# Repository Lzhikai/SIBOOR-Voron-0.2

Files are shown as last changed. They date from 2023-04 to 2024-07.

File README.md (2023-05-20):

# SIBOOR-V0.2

### 0.2-LED-Wiring ：About the wiring of the sibor kit to the hot-side LED.
### Metalsupplements ： Print files not included in the CNC version.
### supplementary ： Unlike the official installation documentation, the installation needs to be done in conjunction with the official documentation and our documentation.

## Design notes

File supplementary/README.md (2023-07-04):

# This guide covers the differences between the SIBOOR 0.2kit and the original VORON0.2 tutorial, and includes instructions on wiring and debugging.
# The supplement also contains the differences section of Siboor V0.2. updated 2023/7/4
# You can download and view the official PDF assembly tutorial of VORON here：[Voron-0.2/Manuals](https://github.com/VoronDesign/Voron-0/tree/Voron0.2/Manuals)  · GitHub
***Github SIBOOR V0.1 kit assembly manual instruction.***

* Page 13-15  ：In SIBOOR V0.2 kit, EXTRUSION A and EXTRUSION B are combined into one EXTRUSION, both of which have been tapped and are common to each other. C EXTRUSION and H EXTRUSION are combined into one EXTRUSION, both of which are drilled and tapped, which are common to each other.

* Page18 ：The SIBOOR V0.2 kit uses the guide strip of purple PCB, so it does not need to use the printed parts and embedded M2 nut.

* Page23 ：SIBOOR V0.2 kit is not equipped with NO DROP NUTS

* Page 20、24 和 113  ：As described above, two purple PCBs are used as guide rail fixing strips to fix the MGN7 guide rail.

* Page 48  ： The SIBOOR V0.2 kit is already equipped with a soldered Endstop, plug and play.

* Page154 ：Make sure that the bearing is flush with the shaft, otherwise it will cause friction between the metal shaft and the motor. Place the side of the bearing flat on the table and press the white gear with both thumbs to make the bearing flush with the shaft.

* Page126 ：In addition to using double-sided adhesive tape to fix the power supply, you can also choose to install two M3 × 6 screws on the reverse side to fix the power supply.

* Page142 ：For SIBOOR V0.2 kit, the heating bed has already lifted the prefabricated fuse. please skip this step

* Page173 ：Use 4 pieces of M2.5×8 screws to fix the CHC V6 hot end

* Page 184  ：SIBOOR V0.2 kit, using a two in one Gemini motherboard, using four nylon posts and M3 × 8 Screws are fixed on the acrylic panel.

* Page 199- 205 ：See the SIBOOR V0.2 kit supplementary instructions separatel

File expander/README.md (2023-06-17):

[Voron-Hardware_STM32_Mini12864](https://github.com/VoronDesign/Voron-Hardware/tree/master/STM32_Mini12864)
# Modified by Wind zhu  , expander.stl
### 3(1mm).stl and 3(2mm).stl are optional.
### just choose one of them to print as 1mm may be too thin and bend easily, the choice is yours

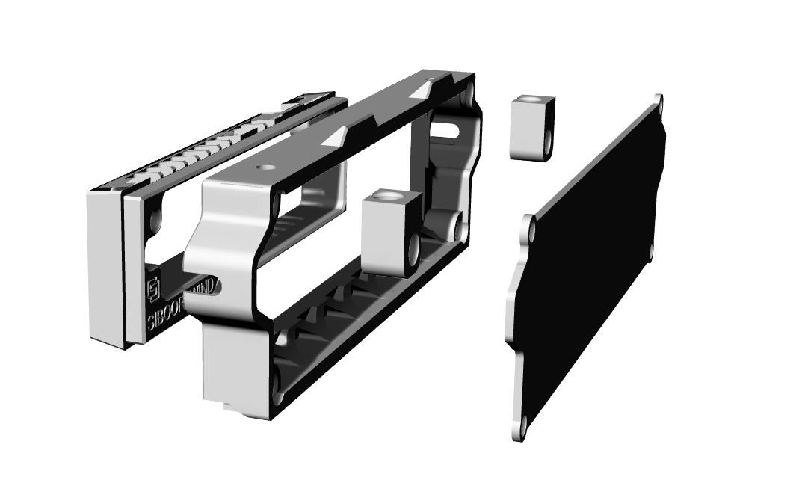
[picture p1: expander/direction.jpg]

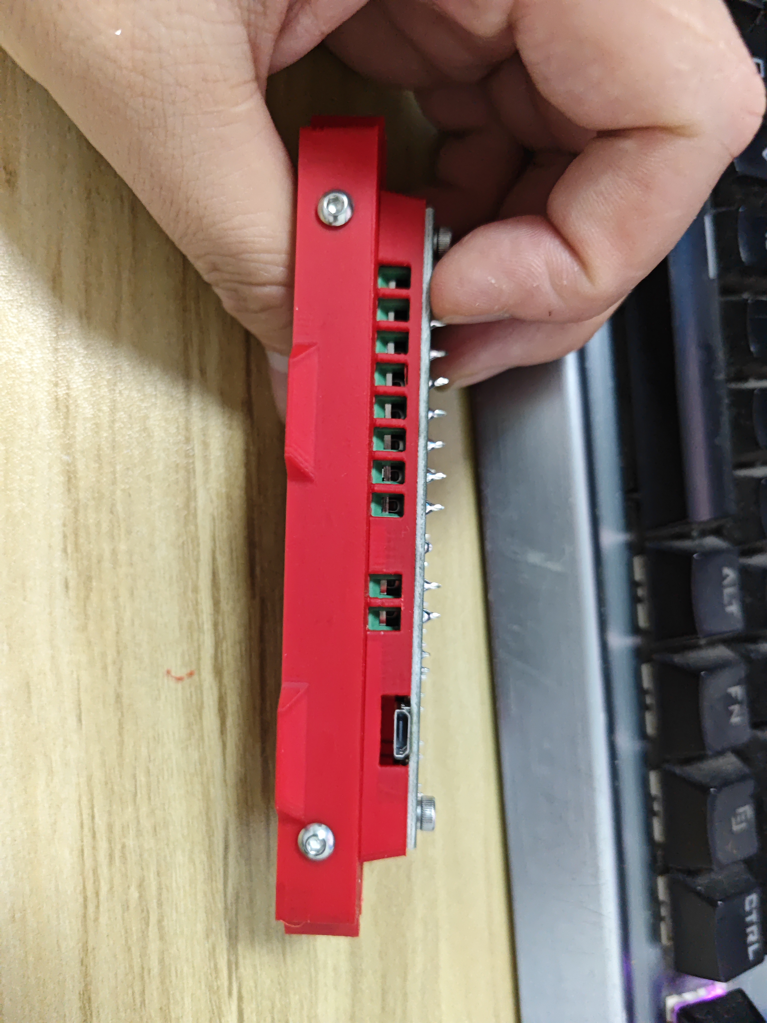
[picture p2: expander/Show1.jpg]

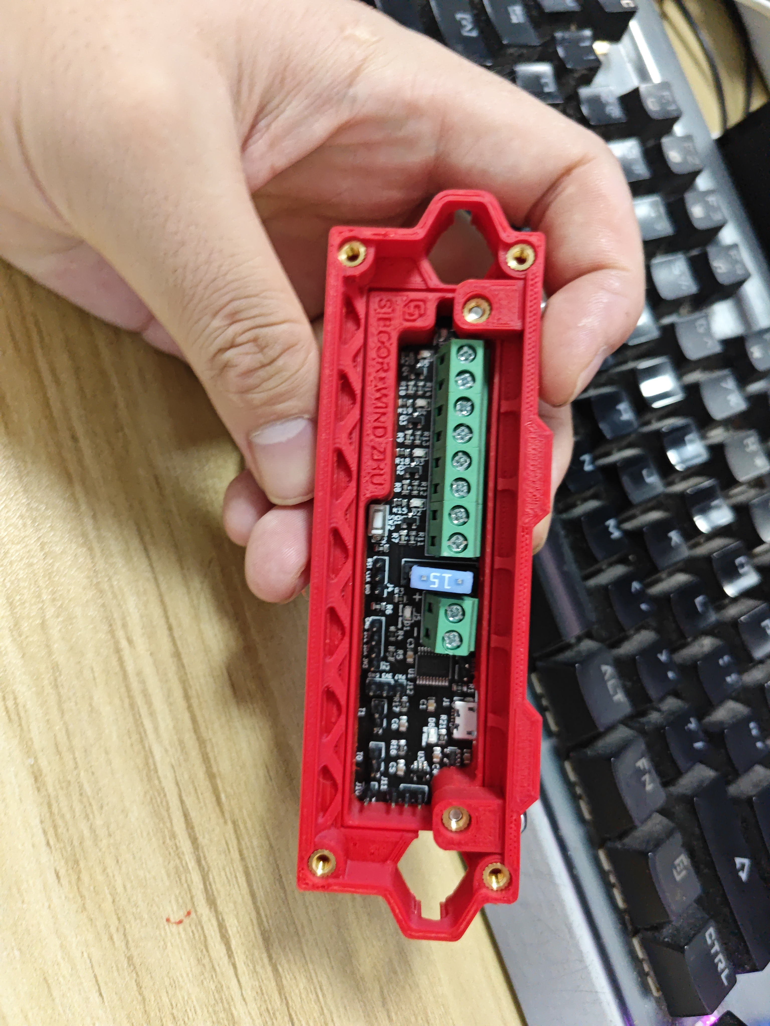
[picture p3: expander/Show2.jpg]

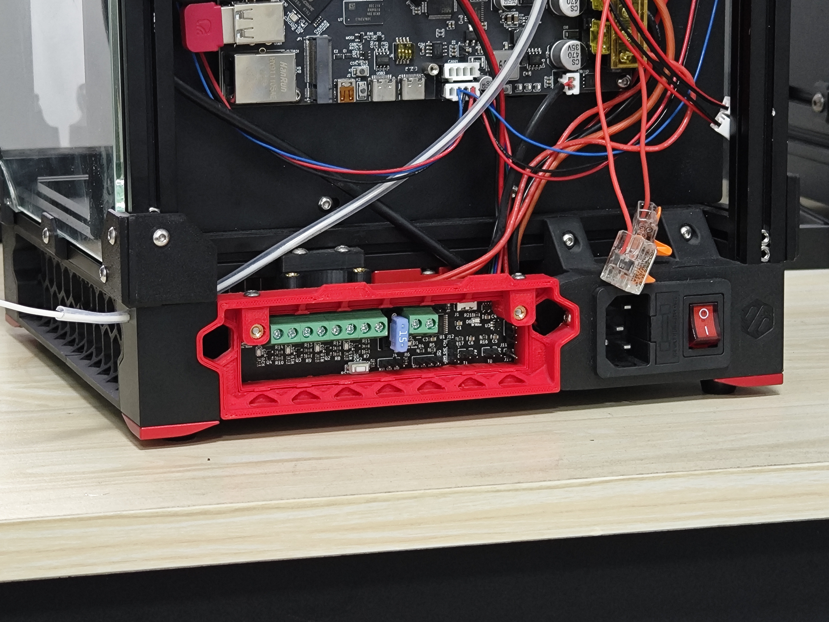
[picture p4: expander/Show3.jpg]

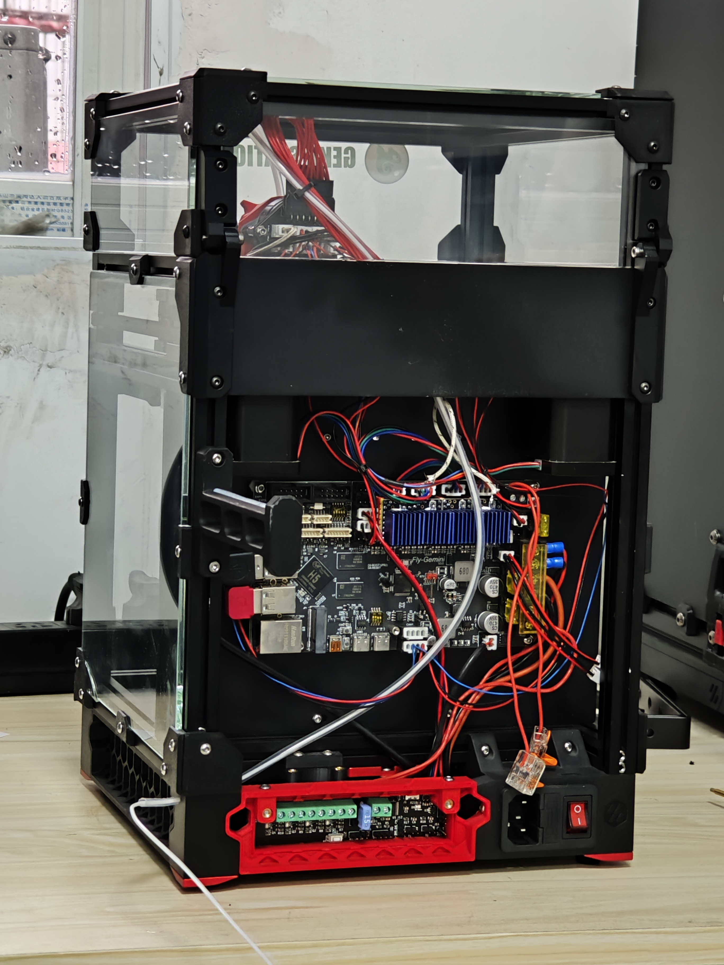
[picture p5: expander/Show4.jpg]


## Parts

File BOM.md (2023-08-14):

# SIBOOR-Voron 0.2 R1 Bom list 
### This list only for reference.  
### Under special situations, parts will updated to same level and quality products.  
### If there has any changes, will update immediately here.
## VORON 0.2 R1 Revision 1.2

| Category | Description | brand | Qty | update time |
|---|---|---|-----|---|
| R1 version | Micro Switch with cable | SIBOOR | 1 | 7/3/23 |
| R1 version | MR85 Bearing | SIBOOR | 1 | 7/3/23 |
| other | Metal rail fixing strip | SIBOOR | 5 | 5/10/23 |
| other | Custom High Speed Steel M1.5/M2.0/ Cross Screwdriver | SIBOOR | 1 | 5/10/23 |
| other | Mini Stealthburner LED light（2 meters with PTFE leads） | SIBOOR | 1 | 4/19/23 |
| other | One out two fan extension cable（PTFE） | / | 1 | 4/21/23 |
| other | Black M3 Metal Internal Thread Stud | / | 2 | 4/1/23 |
| other | Allen wrench (one M2/M3 each) | / | 1 | 3/1/23 |
| Fasteners | 3x6x0.5 Shim Washer | Nickel plating 10.9 | 55  | 4/17/23 |
| Fasteners | M2 Nut | Nickel plating 10.9 | 64  | 3/1/23 |
| Fasteners | M3 Nut | Nickel plating 10.9 | 161 | 3/1/23 |
| Fasteners | M2x6 SHCS | Nickel plating 10.9 | 81  | 3/1/23 |
| Fasteners | M2x6 FHCS | Nickel plating 10.9 | 12  | 3/1/23 |
| Fasteners | M2x8 SHCS | Nickel plating 10.9 | 12  | 3/1/23 |
| Fasteners | M3x6 BHCS | Nickel plating 10.9 | 54  | 3/1/23 |
| Fasteners | M3x8 BHCS | Nickel plating 10.9 | 133 | 3/1/23 |
| Fasteners | M3x8 FHCS | Nickel plating 10.9 | 6 | 3/1/23 |
| Fasteners | M3x10 BHCS | Nickel plating 10.9 | 50  | 4/17/23 |
| Fasteners | M3x12 BHCS | Nickel plating 10.9 | 29  | 3/1/23 |
| Fasteners | M3x16 BHCS | Nickel plating 10.9 | 12  | 3/1/23 |
| Fasteners | M3x25 BHCS | Nickel plating 10.9 | 12  | 3/1/23 |
| Fasteners | M3x30 BHCS | Nickel plating 10.9 | 12  | 3/1/23 |
| Fasteners | M3x35 BHCS | Nickel plating 10.9 | 35  | 3/1/23 |
| Fasteners | M3x40 BHCS | Nickel plating 10.9 | 12  | 3/1/23 |
| Fasteners | M2x10 Self Tapping Screws for Plastic | Nickel plating 10.9 | 35  | 3/1/23 |
| Fasteners | M3 Brass heatstake inserts - short M3x5x4 | / | 58  | 3/1/23 |
| Fasteners | M3 t-nut | / | 2 | 3/1/23 |
| Fasteners | F623-RS Bearing | / | 24  | 3/1/23 |
| Fasteners | yellow die springs 8x4x20mm | / | 3 | 3/1/23 |
| Fasteners | Little Rubber Feet | / | 4 | 3/1/23 |
| Fasteners | 6mm x 3mm Round Neodymium Magnets | / | 8 | 3/1/23 |
| Fasteners | Hexagonal nylon screw post | / | 4 | 3/1/23 |
| Fasteners | BMG Extruder Kit（30 teeth reduction gear is SIboor CNC version） | / | 1 | 8/1/23 |
| Frame | EXTRUSION 15x15 200mm | SIBOOR | 16  | 3/1/23 |
| Frame | EXTRUSION 15x15 100mm | SIBOOR | 3 | 3/1/23 |
| Electronics | LM200-20B24R2 200W Power |  Mornsun | 1 | 3/1/23 |
| Electronics | Gemini V3 board | Mellow | 1 | 3/1/23 |
| Electronics | TMC2209 drivers | / | 4 | 3/1/23 |
| Electronics | SanDisk MicroSD Card 32GB | Sandisk | 1 | 3/1/23 |
| Electronics | USB WIFI module | Tencent | 1 | 3/1/23 |
| Electronics | NEMA14 Stepper Motor 40Ncm | SIBOOR | 2 | 3/1/23 |
| Electronics | NEMA17 Stepper Motor w/ integrated lead screw 200mm T8x8 | SIBOOR | 1 | 3/1/23 |
| Electronics | NEMA14 36mm pancake Motor with 10 tooth gear | MOON‘S | 1 | 3/1/23 |
| Electronics | 3010 blower fans 24V | GEEK | 2 | 3/1/23 |
| Electronics | 3010 axial fan 24V | GEEK | 2 | 3/1/23 |
| Electronics | Micro Switch with cable | / | 1 | 3/1/23 |
| Electronics | C13 Power Cord | / | 1 | 3/1/23 |
| Electronics | IEC320 C14 inlet | / | 1 | 3/1/23 |
| Electronics | CHC V6 Hotend | SIBOOR | 1 | 3/1/23 |
| Electronics | V0-Display | SIBOOR | 1 | 3/1/23 |
| Electronics | 3M 5952 VHB tape | / | 1 | 3/1/23 |
| Electronics | High Flex Wire 20gauge | / | 2 | 3/1/23 |
| Electronics | 7mm x 7mm cable chain (less than 1/2 meter needed) | / | 1 | 3/1/23 |
| Electronics | ADXL345 | SIBOOR | 1 | 3/1/23 |
| Electronics | PTFE cable 0.5M | SIBOOR | 1 | 7/3/23 |
| Electronics | Nylon Cable Ties (1.8mm wide or smaller) | / | 50  | 3/1/23 |
| Motion | MGN7H Linear Rail with Carriage - 150mm(nickel plated) | SIBOOR | 5 | 4/1/23 |
| Motion | GT2 20T (5mm ID 6mm W) | SIBOOR | 2 | 3/1/23 |
| Motion | GT2 Open Belt (6mm W) - 3000mm | GATES | 3 | 3/1/23 |
| Motion | Silicone DC 24V Heater 100x100mm 60W | SIBOOR | 1 | 3/1/23 |
| Buildplate | PEI + 3M 468MP (200MP) | SIBOOR | 1 | 3/1/23 |
| Panels | Acrylic Sheet Clear - 212x230x3mm | / | 2 | 3/1/23 |
| Panels | Acrylic Sheet Clear - 212x239x3mm | / | 1 | 3/1/23 |
| Panels | Upper Rear Panel 212x63x3mm | / | 1 | 3/1/23 |
| Panels | Lower Rear Panel 212x185x3mm | / | 1 | 3/1/23 |
| Panels | Deck Panel 3mm thick (See DXF) | / | 1 | 3/1/23 |
| Panels | Motor Panel 3mm thick (See DXF) | / | 1 | 3/1/23 |
| Panels | Bottom Panel 3mm thick (See DXF) | / | 1 | 3/1/23 |
| Panels | Mid Panel 3mm thick (See DXF) | / | 1 | 3/1/23 |
| Misc. | Bowden Tube 4x2mm - 1m | / | 1 | 3/1/23 |
| Misc. | Bowden Tube 4x3mm - 1m | / | 1 | 3/1/23 |
| Extrusion Tophat | Top Panel 212x212mm | / | 1 | 3/1/23 |
| Extrusion Tophat | Side Panels 212x71mm | / | 4 | 3/1/23 |
| Extrusion Tophat |  EXTRUSION 15x15 200mm | SIBOOR | 4 | 3/1/23 |
| Extrusion Tophat | EXTRUSION15x15×80mm | SIBOOR | 4 | 3/1/23 |
| prints | Full set of prints（ABS） | R1 version | 1 | 4/20/23 |

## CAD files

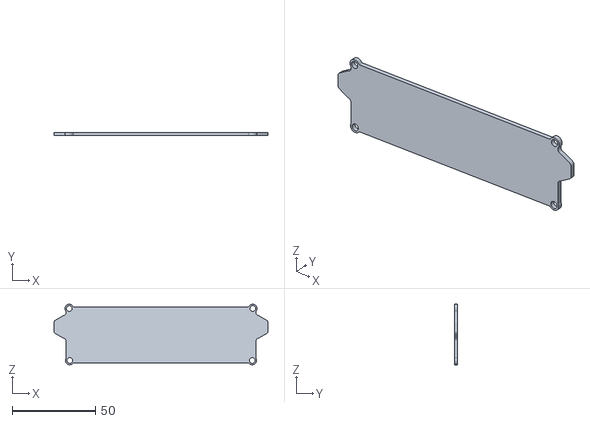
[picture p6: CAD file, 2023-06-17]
expander/3(2mm).stl
128.5 x 2.08 x 36.4

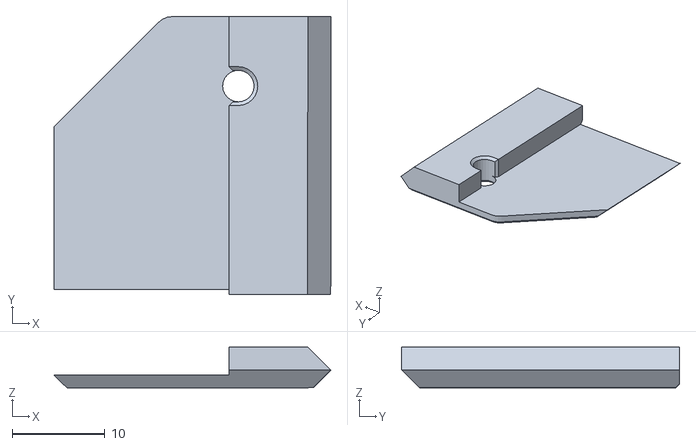
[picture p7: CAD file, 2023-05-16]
Metalsupplements/Panel_Mounting/Rear_Bottom_Right_Clip_x1.stl
29.9 x 30.0 x 4.42

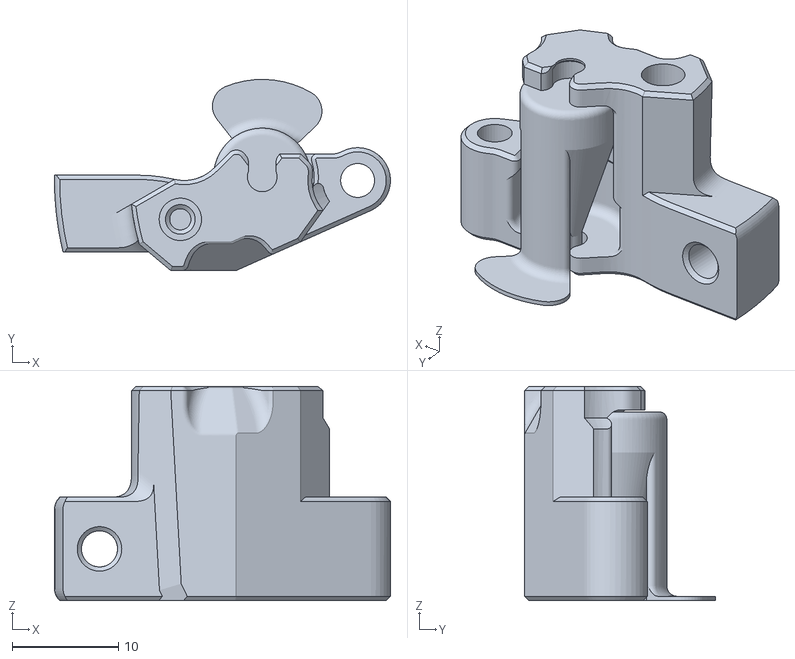
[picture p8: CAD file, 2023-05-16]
Metalsupplements/Toolheads/[a]_Guidler_x1.stl
31.7 x 18.0 x 20.2

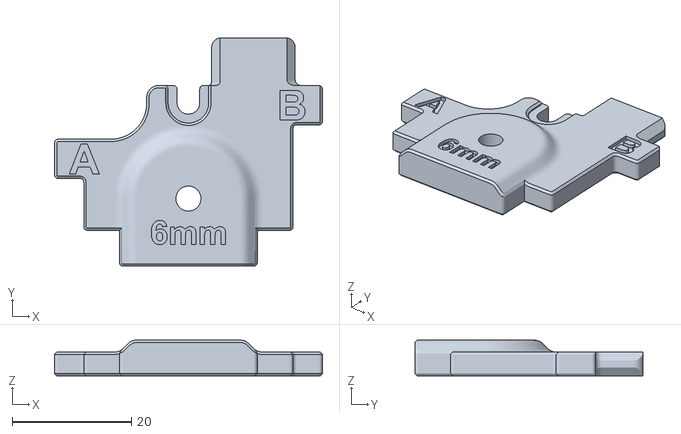
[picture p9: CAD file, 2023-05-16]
Metalsupplements/Tools/Pulley_Jig_V02.stl
44.9 x 38.3 x 6.00

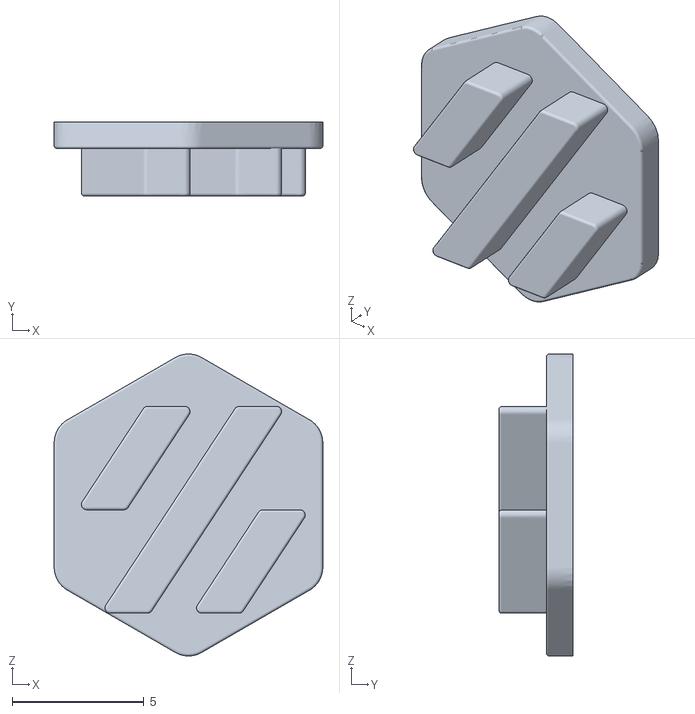
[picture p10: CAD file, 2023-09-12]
STL/AUG NEW/kirigaml/透明灯罩件.stl
10.2 x 2.80 x 11.5

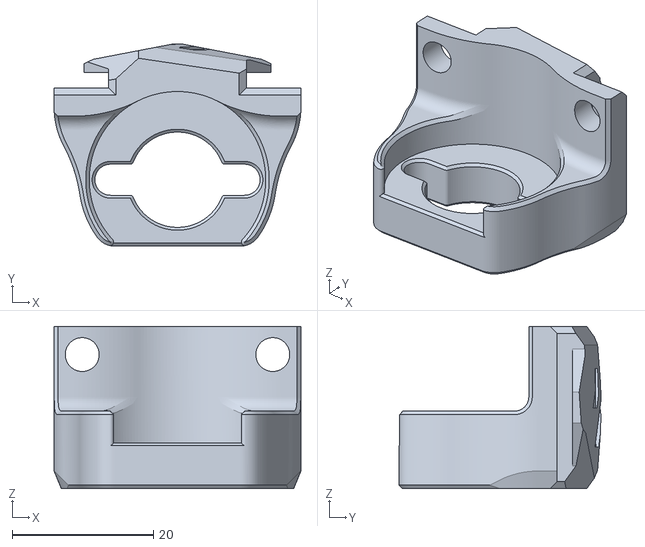
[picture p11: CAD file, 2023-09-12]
STL/AUG NEW/kirigaml/黑色/钣金支架丝杆固定座.stl
35.0 x 28.6 x 23.0

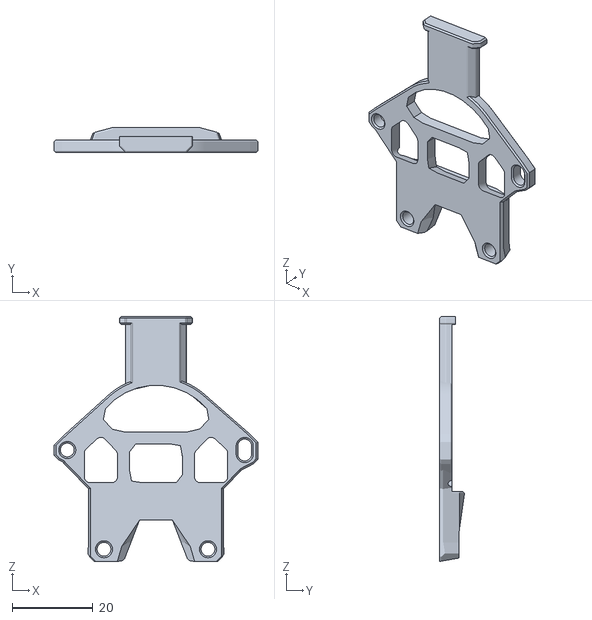
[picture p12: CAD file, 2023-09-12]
STL/AUG NEW/V0-Umbilical/VORON 0.2 转接板背板.stl
50.3 x 6.21 x 60.5

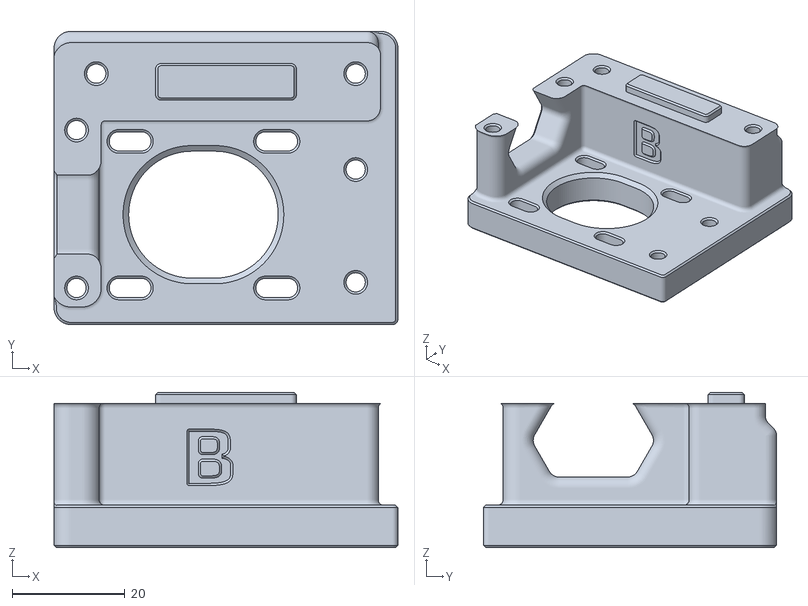
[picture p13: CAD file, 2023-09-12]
STL/B_Drive_Frame_Lower_x1.stl
61.0 x 52.0 x 27.5

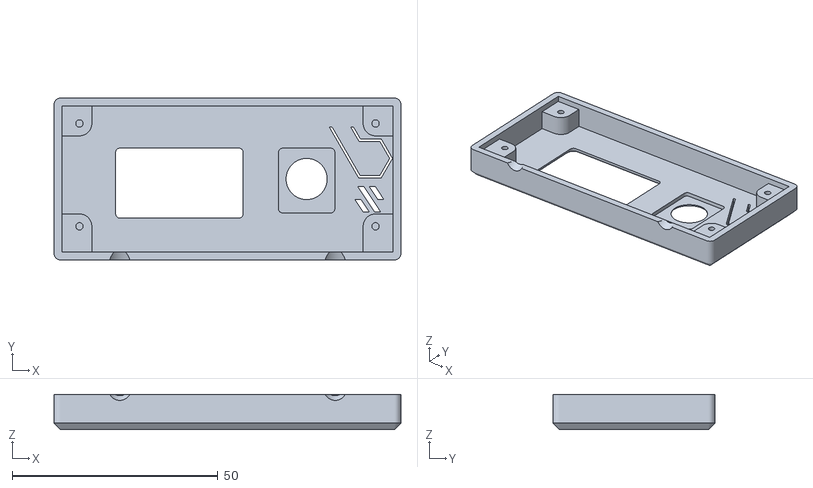
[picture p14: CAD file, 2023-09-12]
STL/Display（显示屏）/[a]_Display_Faceplate_x1.stl
84.4 x 39.4 x 8.63

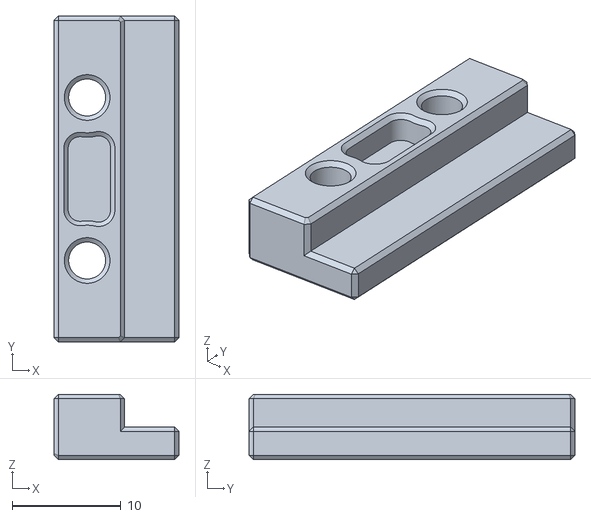
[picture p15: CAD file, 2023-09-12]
STL/Electronics（电气件）/Fan_Mount_Top_x1.stl
11.5 x 30.0 x 6.00

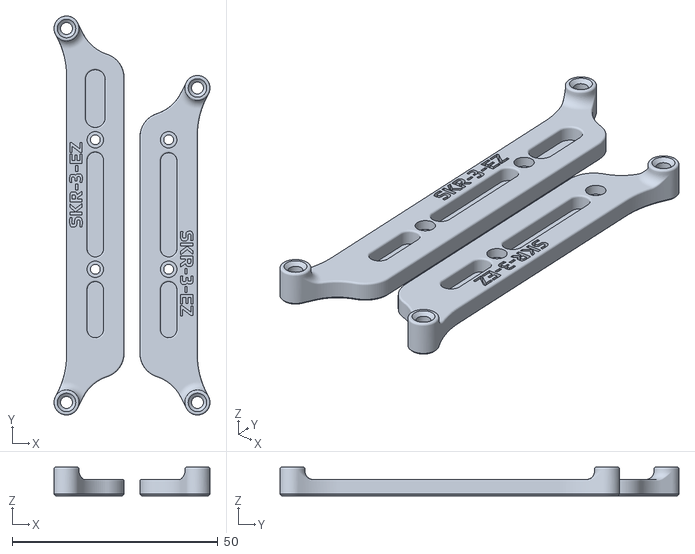
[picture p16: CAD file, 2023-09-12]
STL/Electronics（电气件）/无需打印/SKR_3_EZ_Din_Mount.stl
37.9 x 97.1 x 7.00

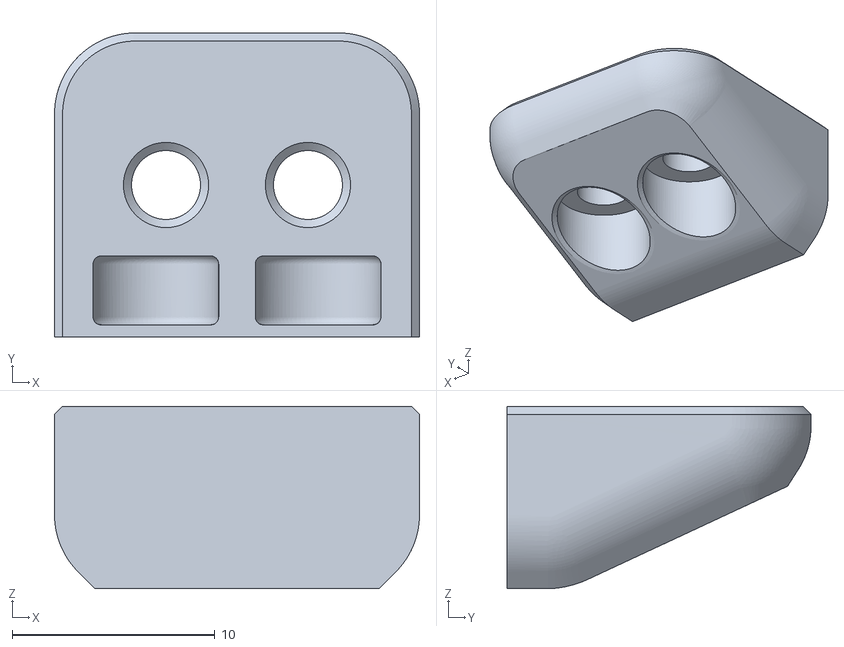
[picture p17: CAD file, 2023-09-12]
STL/Panel_Mounting/把手挡块 ×2.stl
18.0 x 15.0 x 9.00

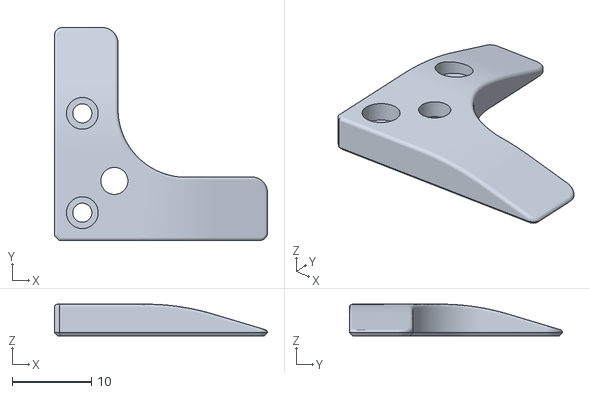
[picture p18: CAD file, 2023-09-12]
STL/Skirts（蜂窝裙边）/[a]_Foot_Accent_B_x2.stl
26.8 x 26.8 x 4.00

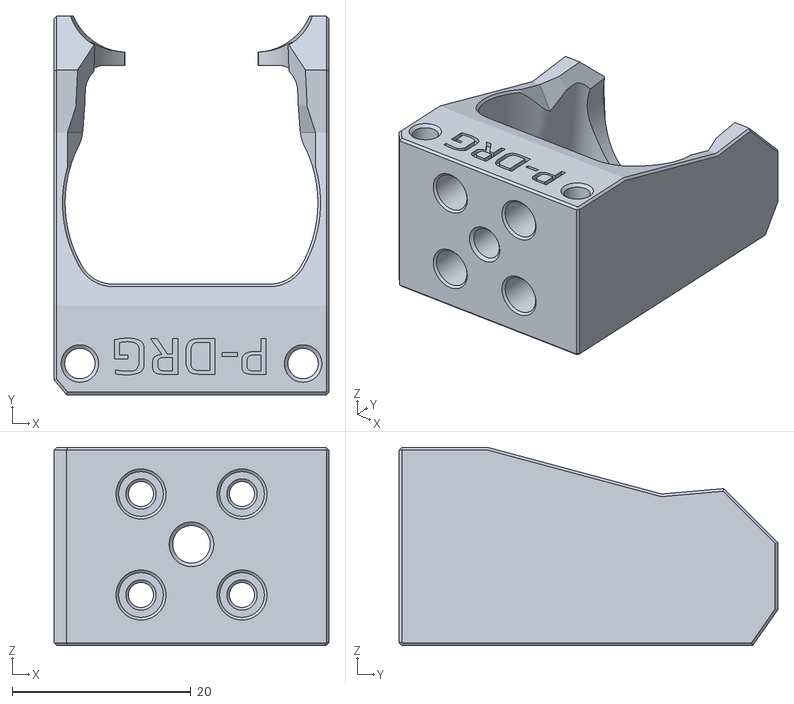
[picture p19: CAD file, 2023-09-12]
STL/Toolheads（工具头）/Hotend_Mounts/Fan_Saver/[a]_FS_Hotend_Mount_Dragon.stl
30.8 x 42.4 x 22.2

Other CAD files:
STL/Toolheads（工具头）/Hotend_Mounts/Fan_Saver/此文件夹内文件不需要打印/[a]_FS_Hotend_Mount_Revo_Voron.stl
STL/Toolheads（工具头）/Hotend_Mounts/（无需打印）Standard/[a]_Hotend_Mount_Drop_Effect_XG.stl
STL/Toolheads（工具头）/Mini_Stealthburner/六角内缩0.1 [a]_MiniSB_Motor_Plate_x1.stl
STL/Tools（工具）/Pulley_Jig_V0.stl
Metalsupplements/Display/Display_Knob_x1.stl
Metalsupplements/Display/Display_Mount_Left_x1.stl
Metalsupplements/Display/Display_Mount_Right_x1.stl
Metalsupplements/Display/[a]_Display_Faceplate_x1.stl
Metalsupplements/Display/[c]_Display_Diffuser.STL
Metalsupplements/Electronics/Fan_Mount_Bottom_x1.stl
Metalsupplements/Electronics/Fan_Mount_Top_x1.stl
Metalsupplements/Electronics/PSU_Cover_x1.STL
Metalsupplements/Panel_Mounting/Door_Latch_x2.STL
Metalsupplements/Panel_Mounting/Front_Bottom_Left_Clip_x1.stl
Metalsupplements/Panel_Mounting/Front_Bottom_Right_Hinge_x1.stl
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

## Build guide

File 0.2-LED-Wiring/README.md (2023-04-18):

## Setting the LED switch：

### Install the LED Effects Library
This will install the LED Effects for Klipper plugin from [here](https://github.com/julianschill/klipper-led_effect)

SSH into your Fly Gemini

account : ```fly```  
password : ```mellow```  

```shell
cd ~
git clone https://github.com/julianschill/klipper-led_effect.git
cd klipper-led_effect
./install-led_effect.sh
```

### Add to printer.cfg  
```
[output_pin LED]
pin: !PB1
pwm: False
```

## Setting the RGB strip:
### Add to printer.cfg 
```
[neopixel my_neopixel]  
pin:PA9 # Main Board Pin Definitions  
chain_count:24 # Number of RGB's   
color_order: GRB # Colour order  
initial_RED: 0.2 # Red Light on default value is 1 max.  
initial_GREEN: 0.2 # Green Light on default value is 1 max.  
initial_BLUE: 0.2 # Blue Light on default value is 1 max.  
  ```
```
[led_effect rainbow]   
leds:    
    neopixel:my_neopixel  
layers:  
  gradient 0.50 0.50 top (1,0,0),(0,1,0),(0,0,1) 
frame_rate: 24  
  
[led_effect extruder_temp]  
leds:  
    neopixel:my_neopixel  
layers:  
    heater 0.50 0.50 top (0.0,1.0,0.0),(1.0,0.0,0.0),(0.0,0.0,1.0)  
frame_rate: 24  
heater: extruder  
autostart: true  
  
[led_effect bed_heating]  
leds:  
    neopixel:my_neopixel  
layers:  
    heater 0.50 0.50 top (0.0,1.0,0.0),(1.0,0.0,0.0),(0.0,0.0,1.0)  
frame_rate: 24  
heater: heater_bed  
autostart: true  
  ```

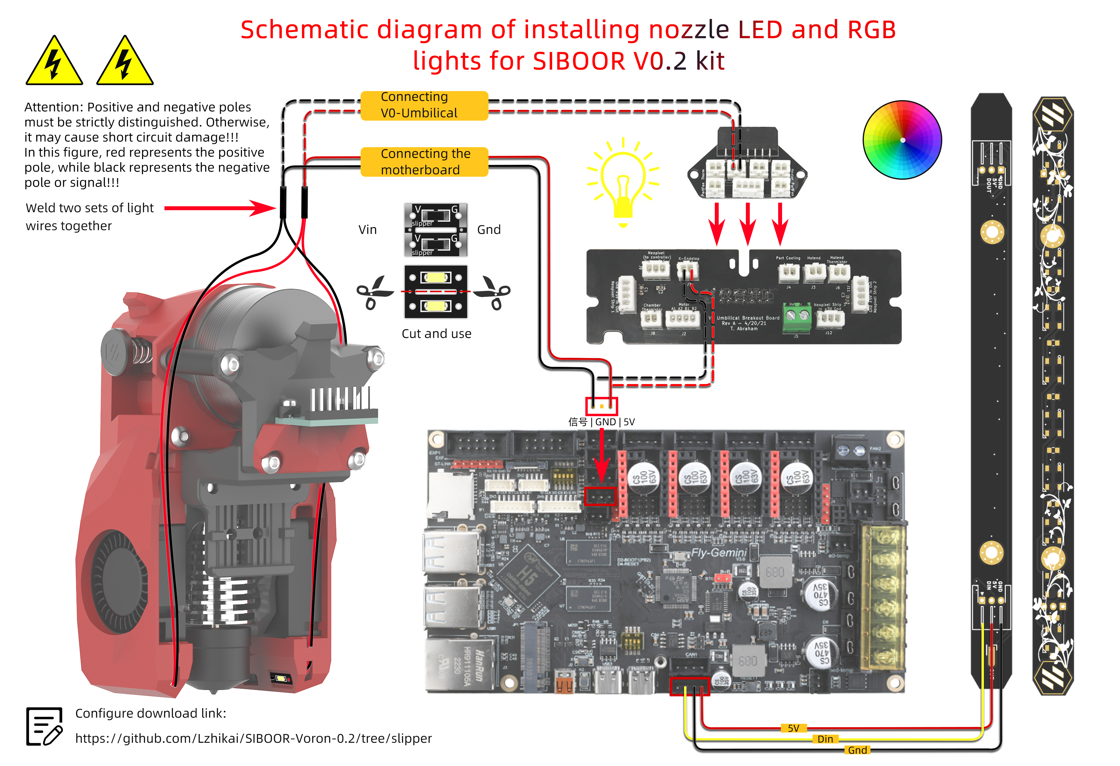
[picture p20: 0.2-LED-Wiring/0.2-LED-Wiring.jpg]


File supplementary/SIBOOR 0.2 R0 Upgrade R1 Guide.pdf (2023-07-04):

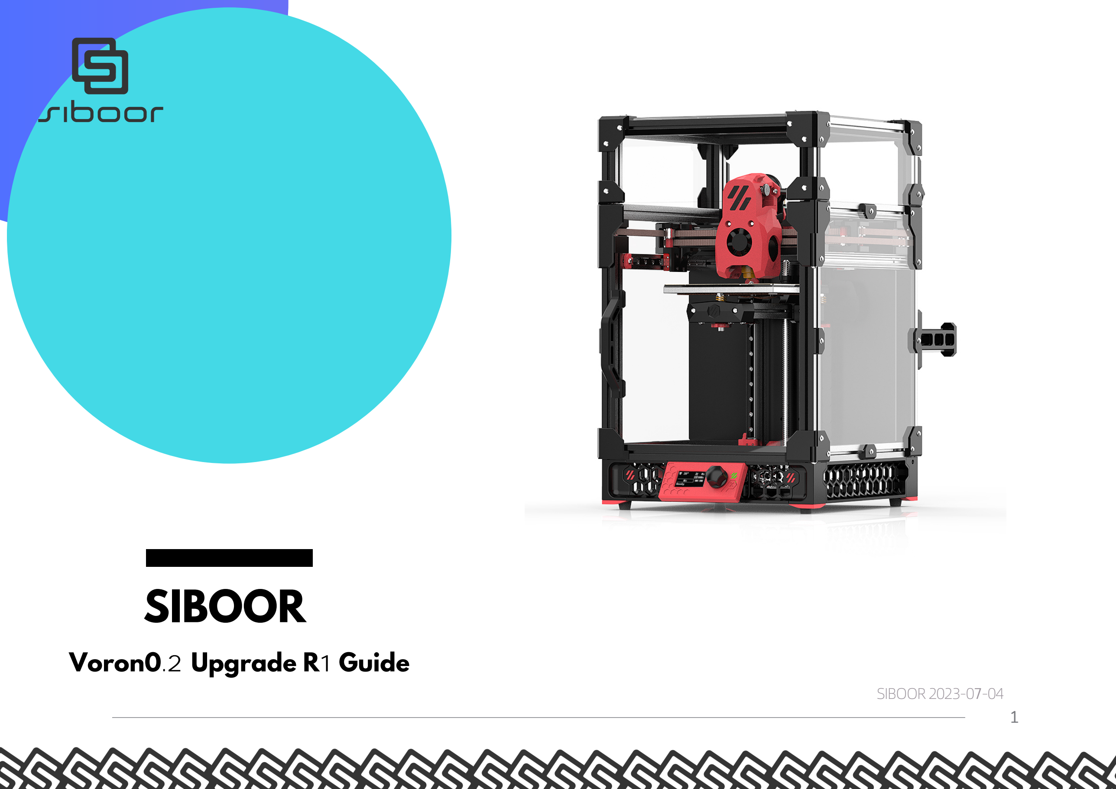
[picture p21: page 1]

1

SIBOOR 2023-0

7-04

# SIBOOR

## Voron0.2 Upgrade R

## 1 Guide

### INTRODUCTION

How to get help
How to find our SIBOOR community, where you can meet many SIBOOR 0.2 users like you
if anyone have any issues do not hesitate to reach out , we welcome suggestions or feedback and we are happy to face and overcome our challanges to improve our products.

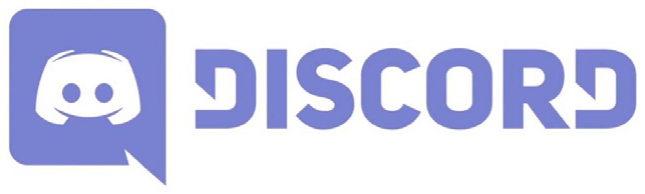
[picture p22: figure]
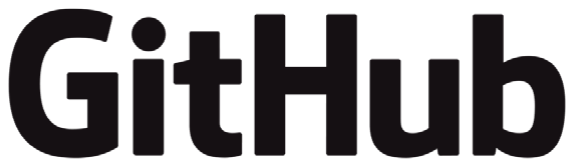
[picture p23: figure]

Voron design：https://www.vorondesign.com/

mellow Fly：https://mellow.klipper.cn/#/

klipper：https://www.klipper3d.org/zh/

Here you can view our database on GITHUB
https://github.com/Lzhikai/siboor-voron

2

https://discord.gg/hpF4bBbrht

### V0.2 R1 (2023 June)

① Skirts

-We fixed the issue where 34mm Z motors didnt fit in the machine with the bottom panel installed, this involved increasing the height of the skirts/ feet by 2mm
-We added a simple filament runout sensor to the rear right foot

② Toolhead

-Mini Stealthburner direct drive and bowden cowling part cooling ducts improved
-an issue with the guidler being able to pivot in an undesired direction was addressed by tightening the bolt holes to reduce play -RIDGA support for the bearings that come stock with the ridga kit has been added

③ Tophat

-cam locks for the tophat were changed to a simple hex key design

④ Z Endstop

-z endstop mount was beefed up to improve ridgidity

BOM Changes the BOM increased by the following items

-2x m2x10 self tapping screw
-1x MR85 bearing
-1x Microswitch
-1x ECAS04 Bowden Collet

https://github.com/VoronDesign/Voron-0

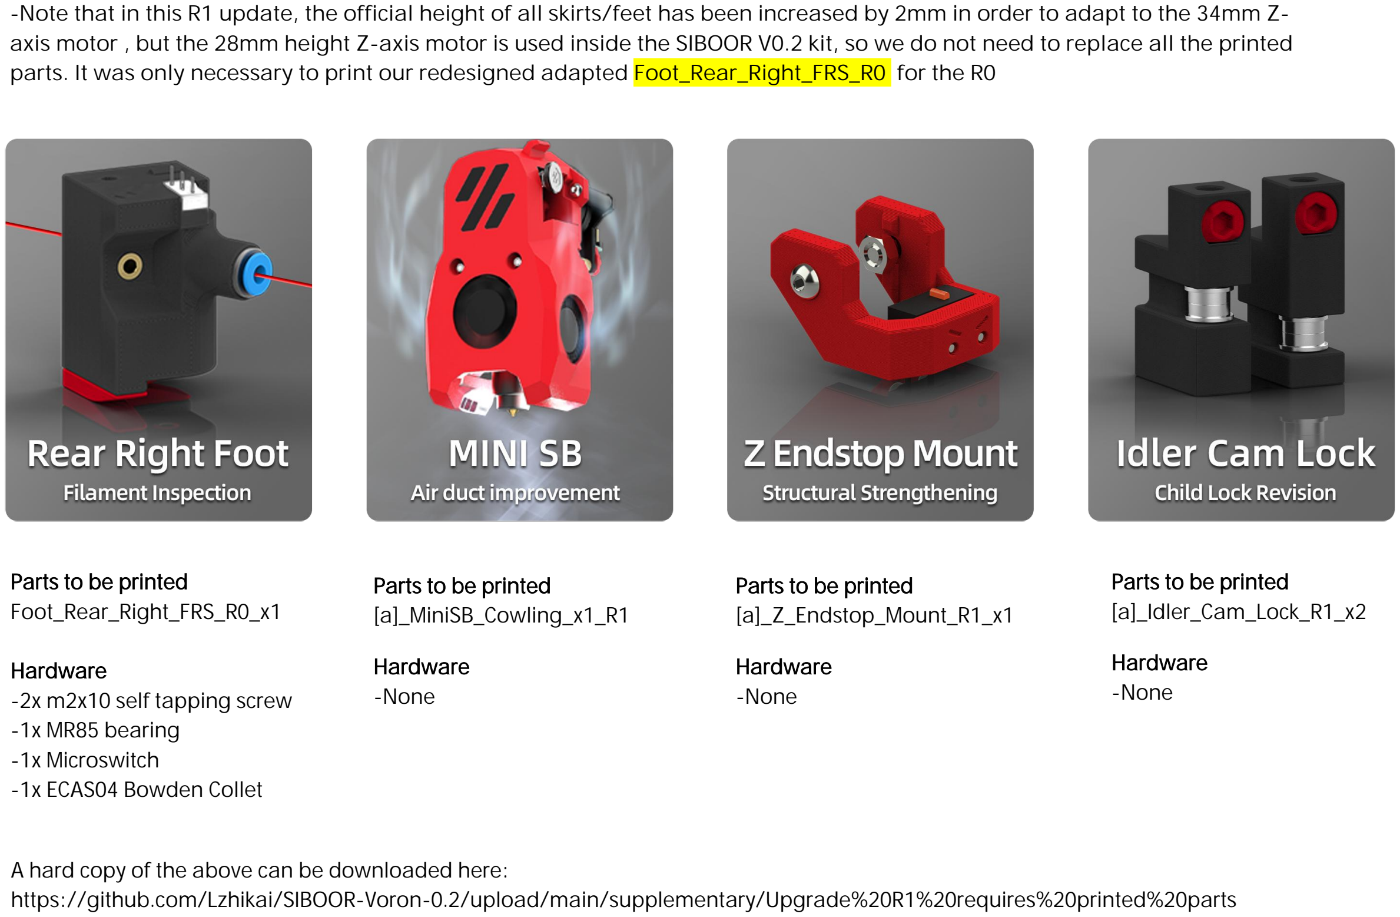
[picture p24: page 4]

-Note that in this R1 update, the official height of all skirts/feet has been increased by 2mm in order to adapt to the 34mm Z-axis motor , but the 28mm height Z-axis motor is used inside the SIBOOR V0.2 kit, so we do not need to replace all the printed parts. It was only necessary to print our redesigned adapted Foot_Rear_Right_FRS_R0 for the R0

Parts to be printed
Foot_Rear_Right_FRS_R0_x1

Hardware
-2x m2x10 self tapping screw -1x MR85 bearing
-1x Microswitch
-1x ECAS04 Bowden Collet

Parts to be printed
[a]_Idler_Cam_Lock_R1_x2

Hardware

Parts to be printed
[a]_Z_Endstop_Mount_R1_x1

Hardware

Parts to be printed
[a]_MiniSB_Cowling_x1_R1

Hardware
-None | -None | -None

A hard copy of the above can be downloaded here: https://github.com/Lzhikai/SIBOOR-Voron-0.2/upload/main/supplementary/Upgrade%20R1%20requires%20printed%20parts

# WHO ARE WE?

# INFINITE PURSUIT OF KNOWLEDGE

## in Chinese , the ultimate and infinite search of thought or knowledge this

is what Siboor stands for.

## We are on a continues pursuit of knowledge, thriving to perfect our products and offering and aim to bring in like minded pioneers into a forward motion towards innovation

and | to | speedup | technological

## advancement in the 3D printing

ecosystem..

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
UIDELINES | SIB

O

O

R

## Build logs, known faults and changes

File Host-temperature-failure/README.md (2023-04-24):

# On the Gemini V3 batch of temperature failure motherboard processing program
According to the answer I got from the official communication with mellow, I roughly sorted out two ways to solve about the host temperature error.

1、The solution from the software is:  

remove the FLY-Gemini temperature sensor inside the printer.cfg    
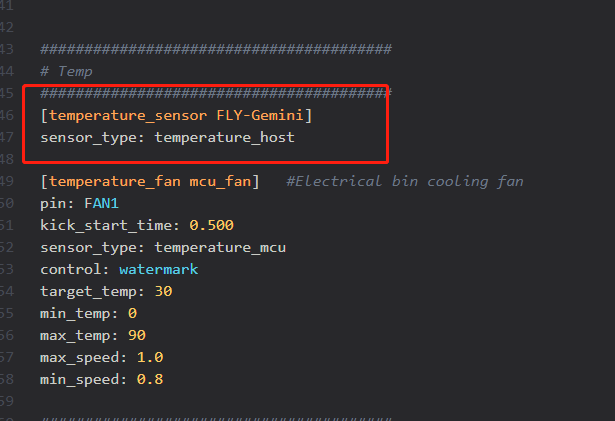
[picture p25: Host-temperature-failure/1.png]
Host-temperature-failure 1! Host-temperature-failure 1


2、The solution in terms of hardware is：

Replace one R8 element above the H5 chip with a "0402 450K 1%" type resistor.   
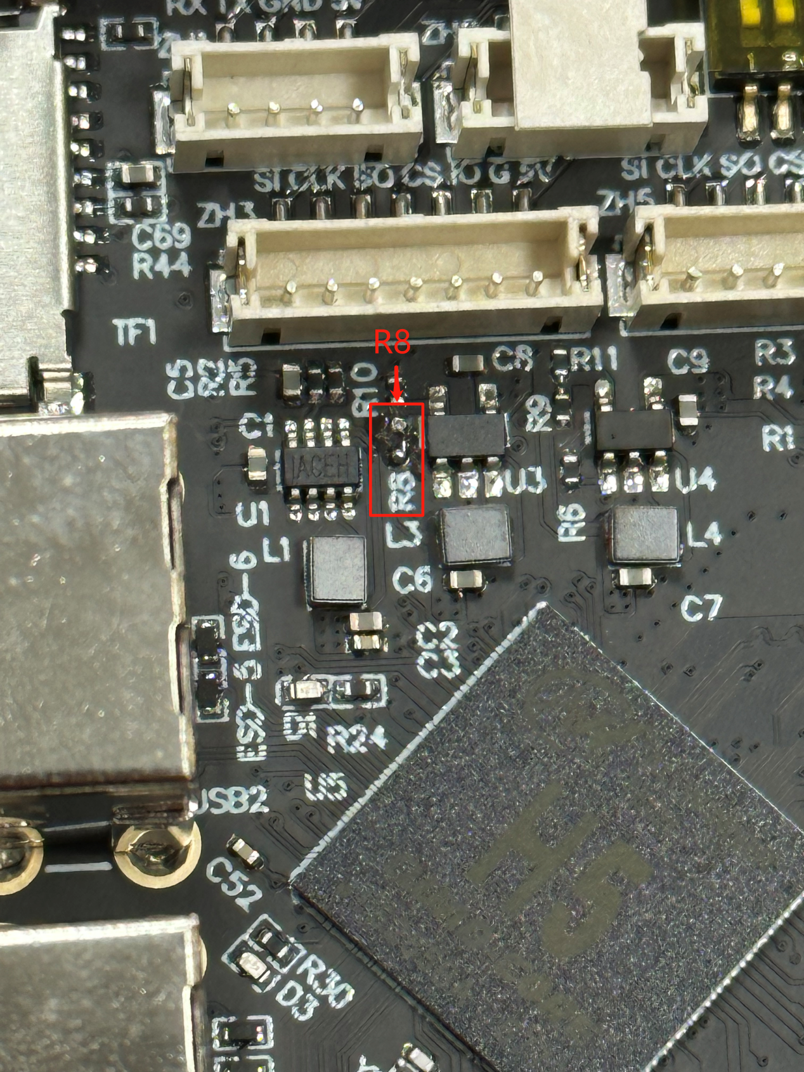
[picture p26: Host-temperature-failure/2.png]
Host-temperature-failure 2! Host-temperature-failure 2


3、Use type-c to power the motherboard, use a multimeter to measure the capacitance value of "C6", the return value of 3.3V is normal.
## ！！！！Be careful not to shake the hands of other accidents occur！！！！  

Host-temperature-failure 3! Host-temperature-failure 3
Host-temperature-failure 4! Host-temperature-failure 4
## Attention：If you are not sure to replace the components, it is recommended to modify the printer.cfg to solve it from the top of the software.

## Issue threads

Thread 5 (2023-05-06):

[Gemini motherboard] smaler screw lenght

kthod861, 2023-05-06:
Hey, not a big deal at all but :

Page 184 ：SIBOOR V0.2 kit, using a two in one Gemini motherboard, using four nylon posts and M3 × 8 Screws are fixed on the acrylic panel.

Only M3 x 6 Screws will work with the provided Hexagonal nylon column height

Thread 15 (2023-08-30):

Missing documentation for ADXL345

cad3na, 2023-08-30:
Maybe I'm missing something, but I can't find any resource to what steps are needed to run input shaper calibration with the provided ADXL345 sensor.

Lzhikai, 2023-08-30:
You can refer to the accelerometer tutorial made by mellow.
https://mellow.klipper.cn/#/advanced/Accelerometer

cad3na, 2023-08-30:
Thank you very much for the quick response! I will give this a try.

d4rxt4r, 2025-07-14:
[mellow.klipper.cn#/advanced/Accelerometer](https://mellow.klipper.cn/#/advanced/Accelerometer)
link does not work anymore... how do i setup adxl with fly-gemnini v3?

Closed 2023-08-30.

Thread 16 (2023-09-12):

Display update

pr0phe, 2023-09-12:
Ive recieved the following once im trying to enable yr display.
How to update it?

MCU Protocol error

This is frequently caused by running an older version of the
firmware on the MCU(s). Fix by recompiling and flashing the
firmware.

Your Klipper version is: v0.11.0-275-g8ef0f7d7
MCU(s) which should be updated:
display: Current version v0.10.0-391-g722ad4a1-dirty-20230510_022857-flygemini
Up-to-date MCU(s):
mcu: Current version v0.11.0-275-g8ef0f7d7

Once the underlying issue is corrected, use the "RESTART"
command to reload the config and restart the host software.

mcu 'display': Unable to encode: config_i2c

Lzhikai, 2023-09-12:
You need to update the display version, refer to the official documentation     https://github.com/VoronDesign/Voron-Hardware/blob/master/V0_Display/Documentation/Setup_and_Flashing_Guide.md

stlfatboy, 2023-12-03:
> You need to update the display version, refer to the official documentation https://github.com/VoronDesign/Voron-
Hardware/blob/master/V0_Display/Documentation/Setup_and_Flashing_Guide.md

Follows flash guide, but ls /dev/serial/by-id/* not showing the device.

Found it boot into DFU mode again.

Using 0.12 klipper

=================================
sudo dfu-util -d ,0483:df11 -R -a 0 -s 0x8000000:leave -D out/klipper.bin

dfu-util 0.9

Copyright 2005-2009 Weston Schmidt, Harald Welte and OpenMoko Inc.
Copyright 2010-2016 Tormod Volden and Stefan Schmidt
This program is Free Software and has ABSOLUTELY NO WARRANTY
Please report bugs to http://sourceforge.net/p/dfu-util/tickets/

dfu-util: Invalid DFU suffix signature
dfu-util: A valid DFU suffix will be required in a future dfu-util release!!!
Opening DFU capable USB device...
ID 0483:df11
Run-time device DFU version 011a
Claiming USB DFU Interface...
Setting Alternate Setting #0 ...
Determining device status: state = dfuERROR, status = 10
dfuERROR, clearing status
Determining device status: state = dfuIDLE, status = 0
dfuIDLE, continuing
DFU mode device DFU version 011a
Device returned transfer size 2048
DfuSe interface name: "Internal Flash "
Downloading to address = 0x08000000, size = 21156
Download [=========================] 100% 21156 bytes
Download done.
File downloaded successfully
dfu-util: Error during download get_status

Failed to flash to 0483:df11: Error running dfu-util

If the device is already in bootloader mode it can be flashed with the
following command:
make flash FLASH_DEVICE=0483:df11
OR
make flash FLASH_DEVICE=1209:beba

If attempting to flash via 3.3V serial, then use:
make serialflash FLASH_DEVICE=0483:df11

make: *** [src/stm32/Makefile:111: flash] Error 255

...
lsusb
Bus 008 Device 001: ID 1d6b:0001 Linux Foundation 1.1 root hub
Bus 005 Device 001: ID 1d6b:0002 Linux Foundation 2.0 root hub
Bus 007 Device 049: ID 0483:df11 STMicroelectronics STM Device in DFU Mode
...

stlfatboy, 2023-12-27:
It seems to be a hardware failure.  Got a new one from seller which works.

Closed 2023-12-27.

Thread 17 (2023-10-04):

0.2-LED-Wiring/README.md

pr0phe, 2023-10-04:
[output_pin LED]
pin: !PB1
pwm: False

By defualt it used in yr config for fly gemini for filament sensor, so doubling PB1 in cfg causes an error in klipper

Lzhikai, 2023-10-04:
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

What is the wrong content?

pr0phe, 2023-10-04:
if you place !PB1 as filament sensor its unable to work as output_pin LED

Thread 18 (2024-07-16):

unsafe default settings

shiftingtech, 2024-07-16:
It is dramatically dangerous to set min_temp:-100 on the extruder and bed, as seen in your printer.cfg

This setting effectively disables the first line of defense against wire breaks or thermistor failures

Lzhikai, 2024-07-16:
This is the lowest temperature, not the highest, so the danger isn't as high as you might think, and you can make one modification since the kit is no longer for sale, so maybe no more changes will be made.

shiftingtech, 2024-07-16:
This is not correct information:  a wire break causes a negative reading.

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

Lzhikai, 2024-07-16:
I'm modifying it now, thanks for the heads up

Lzhikai, 2024-07-16:
Changed it to -10, so I'm about to close the place.

Closed 2024-07-16.

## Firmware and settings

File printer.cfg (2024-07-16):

[include fly_macros.cfg]
[include boards/FLY_GEMINI_V3.cfg]
[include V0Display.cfg]
[mcu]
serial: /dev/serial/by-id/usb-Klipper_stm32f405xx_JKYZ-if00

[mcu host]
serial: /tmp/klipper_host_mcu

[virtual_sdcard]
path: ~/gcode_files

[printer]
kinematics: corexy
max_velocity: 300
max_accel: 3000
max_z_velocity: 5
max_z_accel: 100


########################################
# Temp
########################################
[temperature_sensor FLY-Gemini]
sensor_type: temperature_host

[temperature_fan mcu_fan]   #Electrical bin cooling fan
pin: FAN1                   
kick_start_time: 0.500
sensor_type: temperature_mcu
control: watermark
target_temp: 45.0
min_temp: 0
max_temp: 90
max_speed: 1.0
min_speed: 0.8

########################################
# LED
########################################
[output_pin HE-LED]
pin: host:gpio3
pwm: False

########################################
# filament_switch_sensor
########################################
[filament_switch_sensor DLJC]
pause_on_runout: True
# When set to True, a pause will be executed immediately after a material break
# , if False, a material break pause will not be enabled
runout_gcode: PAUSE
# G-code to be executed after a material break
insert_gcode: RESUME
# G-code to be executed after insertion of consumables
event_delay: 3.0
# Minimum time delay between events, in seconds
pause_delay: 0.5
# Delay between pause commands, scheduling and execution of runout_gcode in seconds
# , increasing delay if strange pause behaviour occurs
switch_pin: !PB1

########################################
# Drives
########################################
[stepper_x]
## Refer to https://docs.vorondesign.com/build/startup/#v0
step_pin: X_STEP
dir_pin: X_DIR
enable_pin: !X_EN
rotation_distance: 40
microsteps: 16
full_steps_per_rotation: 200                                        # Set to 400 for 0.9° degree stepper motor, 200 is for 1.8° stepper motors
endstop_pin: tmc2209_stepper_x:virtual_endstop
position_endstop: 120
position_max: 120
homing_speed: 30                                                    # Can be increased after initial setup, Max 100
homing_retract_dist: 0
homing_positive_dir: true
step_pulse_duration: 0.000001

[stepper_y]
## Refer to https://docs.vorondesign.com/build/startup/#v0
step_pin: Y_STEP
dir_pin: Y_DIR                                                       # Check motor direction in link above. If inverted, add a ! before PC4
enable_pin: !Y_EN
rotation_distance: 40
microsteps: 16
full_steps_per_rotation: 200                                        # Set to 400 for 0.9° degree stepper motor, 200 is for 1.8° stepper motors
endstop_pin: tmc2209_stepper_y:virtual_endstop
position_endstop: 120
position_max: 120
homing_speed: 30                                                    # Can be increased after initial setup, Max 100
homing_retract_dist: 0
homing_positive_dir: true
step_pulse_duration: 0.000001

[stepper_z]
## Refer to https://docs.vorondesign.com/build/startup/#v0
step_pin: Z_STEP
dir_pin: !Z_DIR                                                       # Check motor direction in link above. If inverted, remove a ! before PC4
enable_pin: !Z_EN
rotation_distance: 8                                                # For T8x8 integrated lead screw
microsteps: 32
endstop_pin: Z_STOP
position_endstop: 120
position_max: 120
position_min: -1.5
homing_speed: 120
second_homing_speed: 3.0
homing_retract_dist: 3.0


[extruder]
step_pin: E_STEP
dir_pin: !E_DIR
enable_pin: !E_EN
microsteps: 16
rotation_distance: 23
gear_ratio: 50:10   
nozzle_diameter: 0.400
filament_diameter: 1.750
heater_pin: HEAT
sensor_pin: HEAT_TEMP
sensor_type: ATC Semitec 104GT-2
control: pid
pid_Kp: 22.2
pid_Ki: 1.08
pid_Kd: 114
min_temp: -10
max_temp: 350
min_extrude_temp: 10
step_pulse_duration: 0.000004



########################################
# BED
########################################
[heater_bed]
heater_pin: BED_OUT
sensor_pin: BED_TEMP
sensor_type: ATC Semitec 104GT-2
control: watermark
min_temp: -10
max_temp: 110
max_power: 1.0

########################################
# FANs
########################################
[fan]
pin: FAN0
#cycle_time: 0.50

########################################
# TMC2208 configuration./2209/2225
########################################

[tmc2209 stepper_x]
uart_pin: X_CS
interpolate: False
run_current: 1.0
sense_resistor: 0.110
stealthchop_threshold: 200                          # Set to 999999 to turn stealthchop on, and 0 to use spreadcycle
diag_pin: PA4  										# YOU NEED TO JUMP THIS DIAG PIN ON YOUR BOARD FOR SENSORLESS HOMING TO WORK 
driver_SGTHRS: 70									# 255 is most sensitive value, 0 is least sensitive


[tmc2209 stepper_y]
uart_pin: Y_CS
interpolate: False
run_current: 1.0
sense_resistor: 0.110
stealthchop_threshold: 200                          # Set to 999999 to turn stealthchop on, and 0 to use spreadcycle
diag_pin: PA5 										# YOU NEED TO JUMP THIS DIAG PIN ON YOUR BOARD FOR SENSORLESS HOMING TO WORK 
driver_SGTHRS: 70									# 255 is most sensitive value, 0 is least sensitive

[tmc2209 stepper_z]
uart_pin: Z_CS
run_current: 0.5500
interpolate: False

[tmc2209 extruder]
uart_pin: E_CS
run_current: 0.5500
interpolate: False

#打印开始    
[gcode_macro PRINT_START]
#   Use PRINT_START for the slicer starting script - please customize for your slicer of choice
description: 开始打印
gcode:
    G90
    M107
    M82
    G28
    G1 Z20 F3000
    G92 E0
    G1 X110 Y0.5 F2000
    G1 Z0.28 F400
    G1 X30 Y0.5 E18 F1000
    G1 Z0.5 F200
    G92 E0

    

#打印结束
[gcode_macro PRINT_END]
#   Use PRINT_END for the slicer ending script - please customize for your slicer of choice
gcode:
    M400                           ; wait for buffer to clear
    G92 E0                         ; zero the extruder
    G1 E-4.0 F3600                 ; retract filament
    G91                            ; relative positioning

    #   Get Boundaries
    {% set max_x = printer.configfile.config["stepper_x"]["position_max"]|float %}
    {% set max_y = printer.configfile.config["stepper_y"]["position_max"]|float %}
    {% set max_z = printer.configfile.config["stepper_z"]["position_max"]|float %}

    #   Check end position to determine safe direction to move
    {% if printer.toolhead.position.x < (max_x - 20) %}
        {% set x_safe = 20.0 %}
    {% else %}
        {% set x_safe = -20.0 %}
    {% endif %}

    {% if printer.toolhead.position.y < (max_y - 20) %}
        {% set y_safe = 20.0 %}
    {% else %}
        {% set y_safe = -20.0 %}
    {% endif %}

    {% if printer.toolhead.position.z < (max_z - 2) %}
        {% set z_safe = 2.0 %}
    {% else %}
        {% set z_safe = max_z - printer.toolhead.position.z %}
    {% endif %}

    G0 Z{z_safe} F3600             ; move nozzle up
    G0 X{x_safe} Y{y_safe} F20000  ; move nozzle to remove stringing
    TURN_OFF_HEATERS
    M107                           ; turn off fan
    G90                            ; absolute positioning
    G0 X60 Y{max_y} F3600          ; park nozzle at rear
    SET_SKEW CLEAR=1

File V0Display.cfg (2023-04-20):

[mcu display]
serial: /dev/serial/by-id/usb-Klipper_stm32f042x6_JKYZ-if00
restart_method: command

[display]
lcd_type: sh1106
i2c_mcu: display
i2c_bus: i2c1a
encoder_pins: ^display:PA4, ^display:PA3
click_pin: ^!display:PA1
kill_pin: ^!display:PA5
x_offset: 2

[neopixel displayStatus]
pin: display:PA0
chain_count: 1
color_order: GRB
initial_RED: 0.24
initial_GREEN: 0.02
initial_BLUE: 0.25

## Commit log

2023-04-24 Host temperature failure problem
2023-04-24 Create Host temperature failure problem.md
2023-06-19 Motor voltages on X/Y are too high. reduce them to prevent overheat failures
    [printer.cfg]
2023-07-01 Update R2 configuration
    LED ,filament_switch ,wiring
    [printer.cfg]
2023-07-06 R0 up R1 STL
    [Foot_Rear_Right_FRS_R0_x1.STL, [a]_Idler_Cam_Lock_R1_x2.STL, [a]_Z_Endstop_Mount_R1_x1.STL]
